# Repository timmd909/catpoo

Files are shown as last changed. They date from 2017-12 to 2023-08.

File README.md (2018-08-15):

# Cat Antagonizing Tactical Platform of Oppression (CATPOO)

This project is for my autodidactic hacking pleasure. One of my childhood
dreams was to create a robot like a T-800. One day...

In the meantime, figured it wouldn't be too hard to create a robot that
can antagonize and annoy cats or small dogs.

## Related Repositories

* [CATPOO Drive](git@github.com:timmd909/catpoo-drive.git) - Software
  for Arduinos for controlling all robots.
* [CATPOO Models](git@github.com:timmd909/catpoo-models.git) - FreeCAD
  models of everything necessary to build a CATPOO.

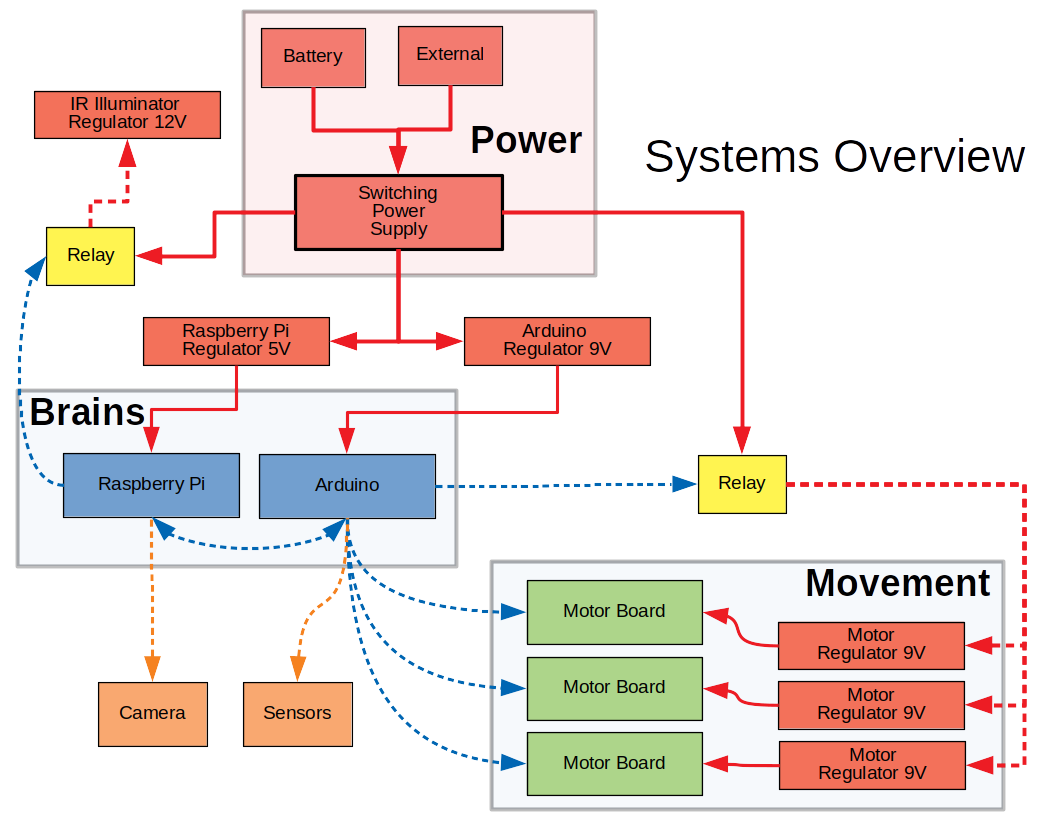
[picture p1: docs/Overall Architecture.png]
Overall architecture


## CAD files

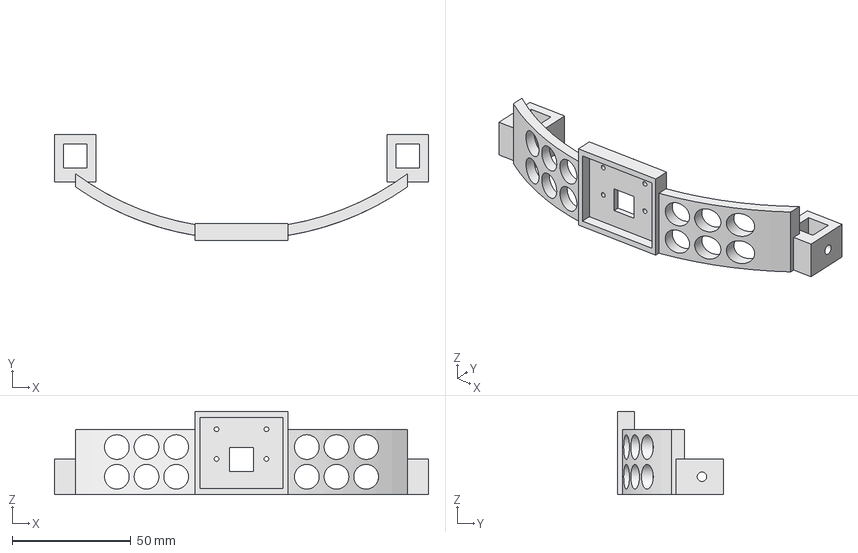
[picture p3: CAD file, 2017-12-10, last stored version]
docs/models/Camera and illuminator.fcstd
157.5 x 44.5 x 35.0 mm

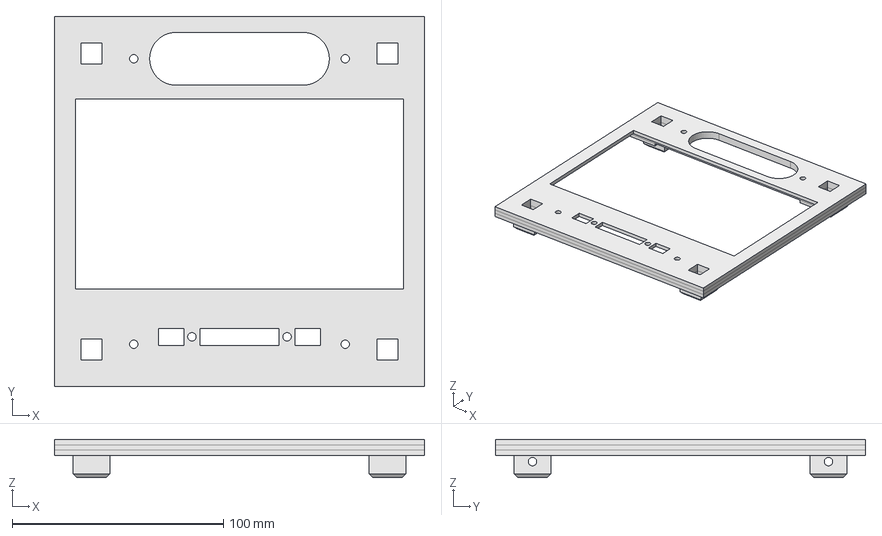
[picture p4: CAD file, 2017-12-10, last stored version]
docs/modular/LCD - top redone.fcstd
175.0 x 175.0 x 18.0 mm

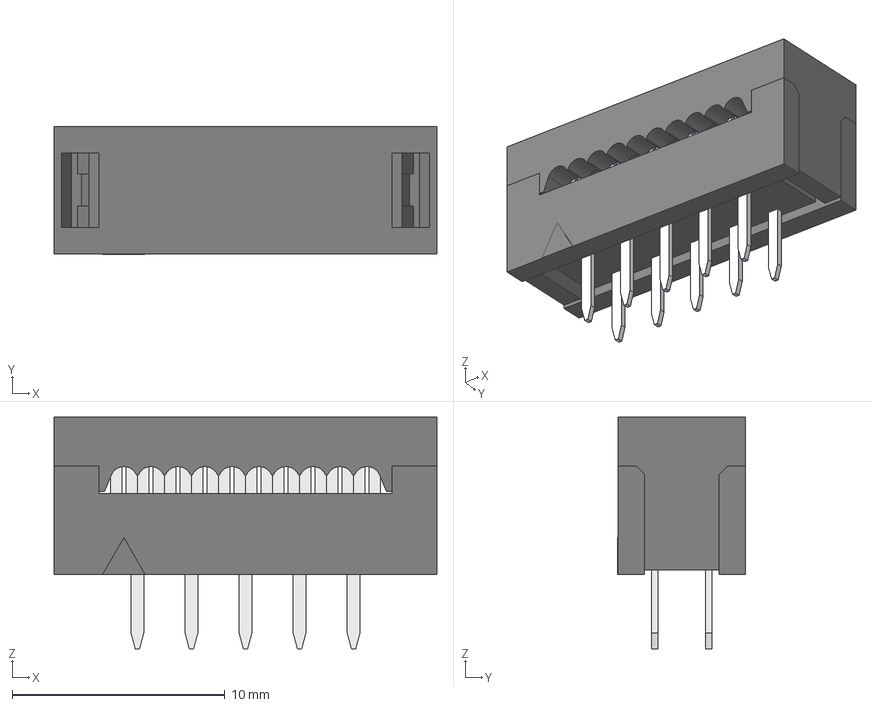
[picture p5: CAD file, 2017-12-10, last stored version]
docs/parts/connectors/direct-wire-2x5.stp
18.0 x 6.03 x 10.9 mm

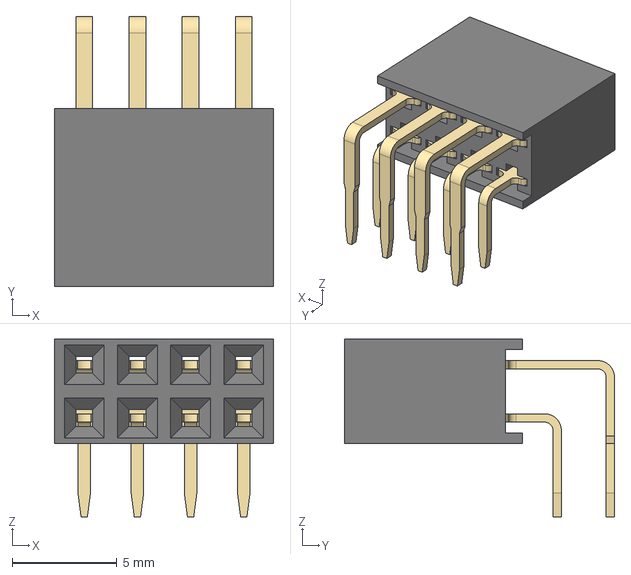
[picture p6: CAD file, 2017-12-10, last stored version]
docs/parts/connectors/female/right_angle/2.54mm/DS1024-2x4RF1.stp
10.5 x 12.9 x 8.50 mm

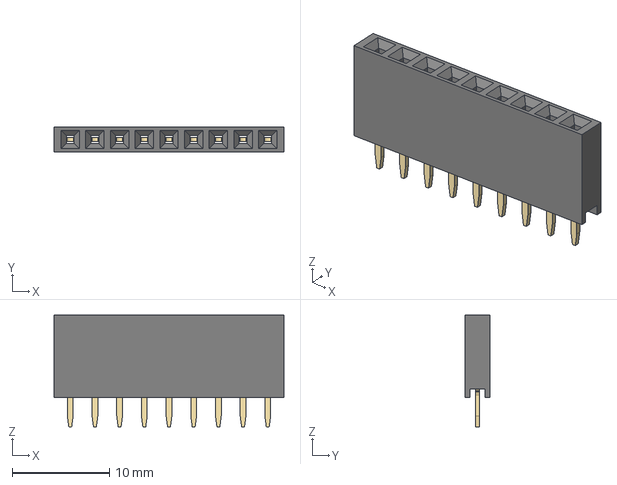
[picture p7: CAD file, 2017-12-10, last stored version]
docs/parts/connectors/female/vertical/2.54mm/DS1023-1x9SF11.stp
23.7 x 2.54 x 11.5 mm

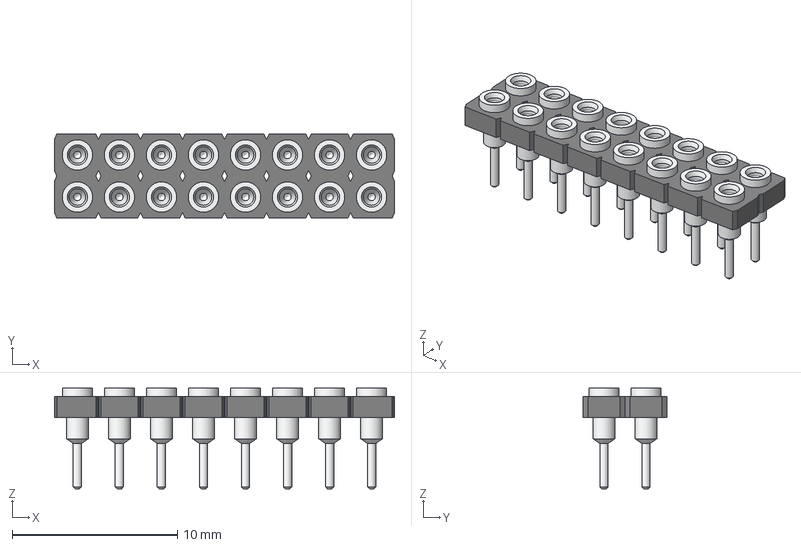
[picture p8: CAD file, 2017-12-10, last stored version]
docs/parts/connectors/female/vertical/2.54mm/Samtec/SDL-108-TT-11.stp
20.6 x 5.08 x 6.10 mm

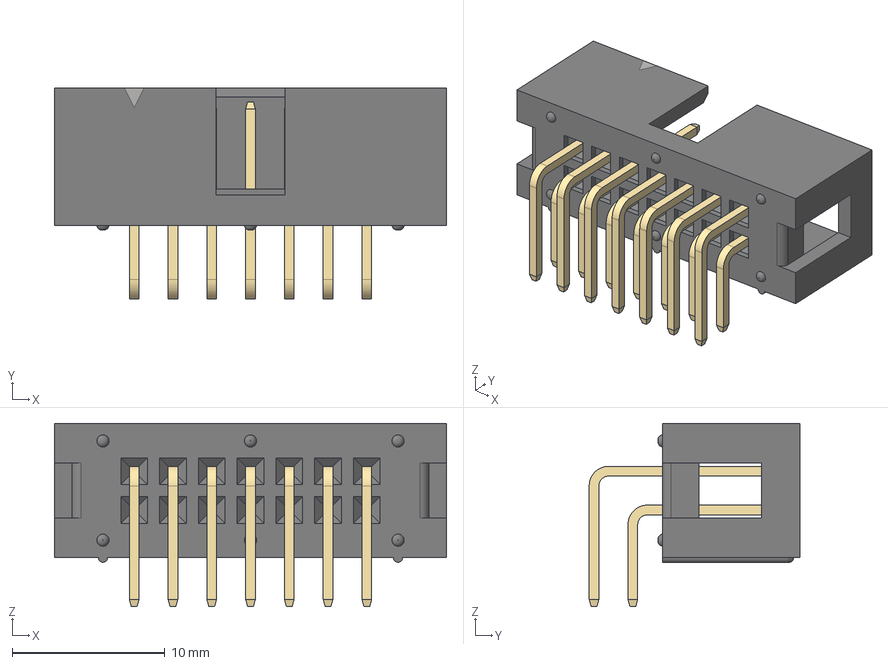
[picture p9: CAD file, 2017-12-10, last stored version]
docs/parts/connectors/male/shrouded/right_angle/2.54mm/DS1013-14RSiB.stp
25.7 x 13.8 x 12.0 mm

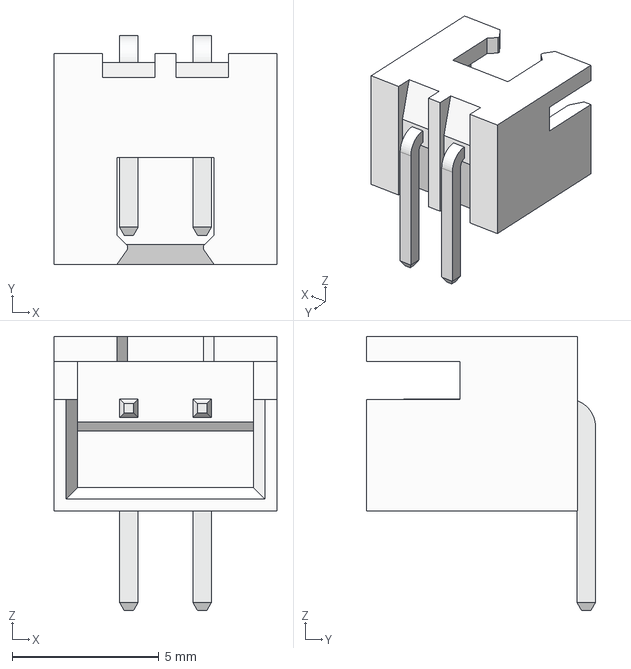
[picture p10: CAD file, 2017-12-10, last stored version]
docs/parts/connectors/male/shrouded/right_angle/2.5mm/DS1069-2MRW6XB.stp
7.60 x 7.82 x 9.35 mm

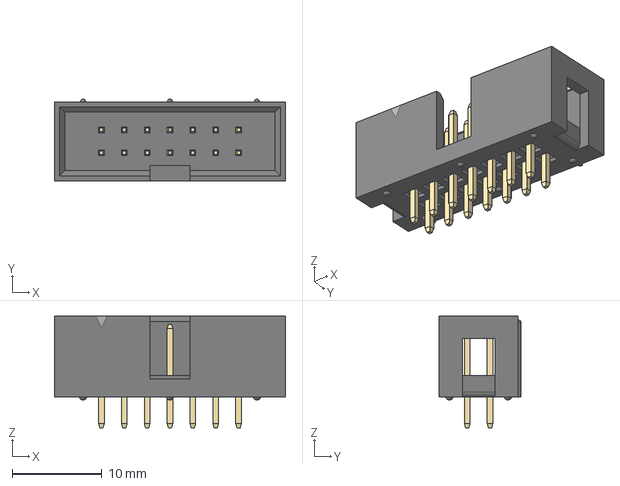
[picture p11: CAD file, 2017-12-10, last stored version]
docs/parts/connectors/male/shrouded/vertical/2.54mm/DS1013-14SSiB.stp
25.7 x 9.10 x 12.4 mm

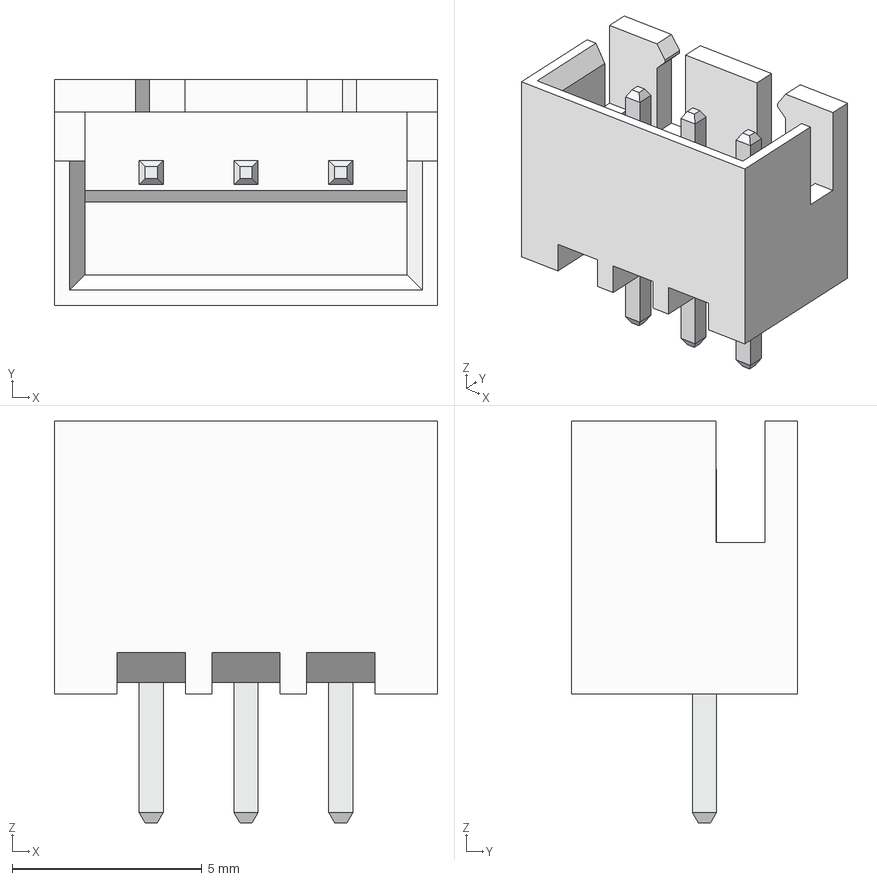
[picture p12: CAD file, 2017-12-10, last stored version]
docs/parts/connectors/male/shrouded/vertical/2.5mm/DS1069-3MVW6X.stp
10.1 x 5.95 x 10.6 mm

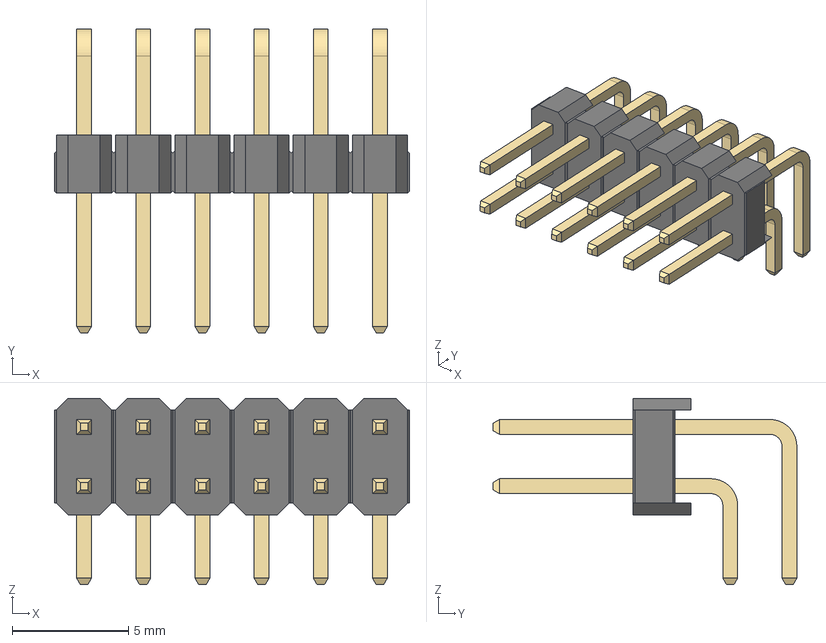
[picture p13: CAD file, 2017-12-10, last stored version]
docs/parts/connectors/male/unshrouded/right_angle/2.54mm/DS1022-2x6RF11.stp
15.2 x 13.0 x 8.00 mm

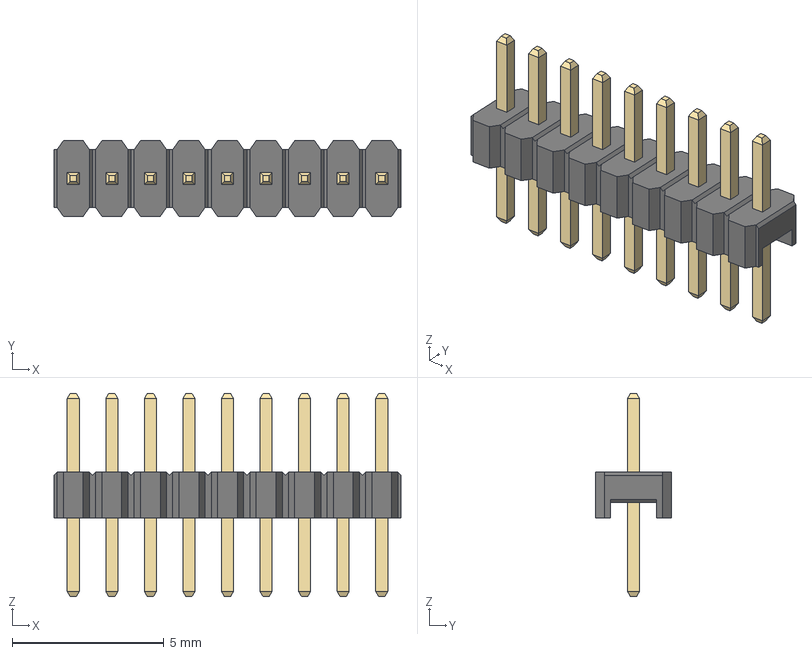
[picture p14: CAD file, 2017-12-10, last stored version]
docs/parts/connectors/male/unshrouded/vertical/1.27mm/DS1031-01-1x9P8BV2-1.stp
11.4 x 2.50 x 6.70 mm

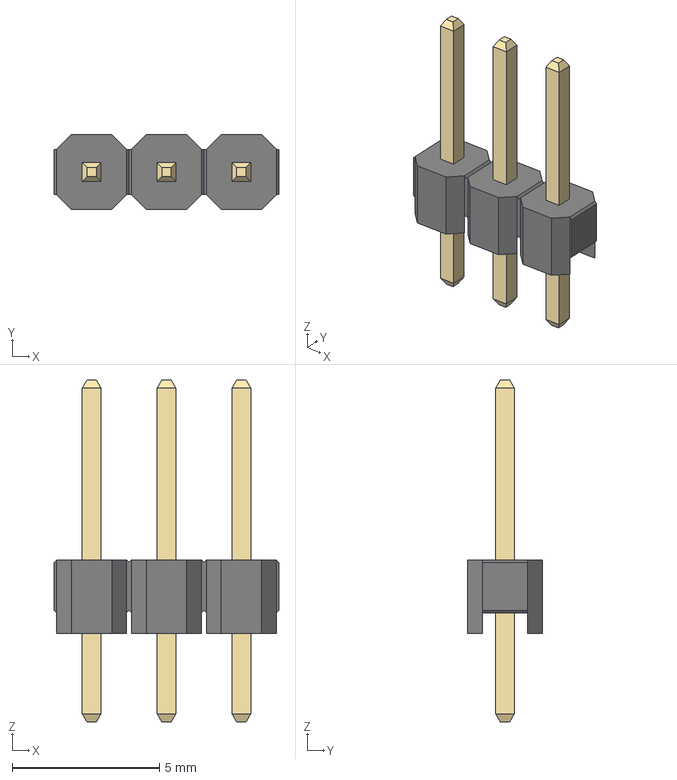
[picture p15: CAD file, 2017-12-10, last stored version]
docs/parts/connectors/male/unshrouded/vertical/2.54mm/DS1021-1x3SF11.stp
7.62 x 2.54 x 11.6 mm

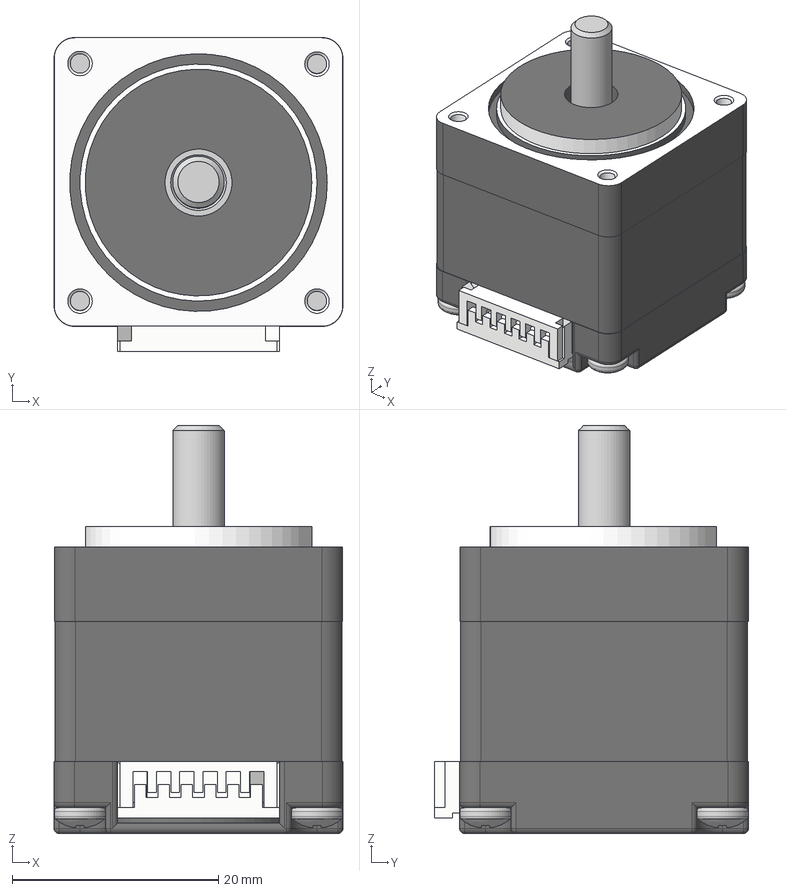
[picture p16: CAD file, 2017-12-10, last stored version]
docs/parts/NEMA 11 Stepper Motor.STEP
28.0 x 30.5 x 39.6 mm
Bottom Cap
695-ZZ Bearing x 2
Centre Housing
Top Cap
Rotor
Rotor Washer
Short Spacer
Long Spacer
M2.5 x 20mm Bolt x 4

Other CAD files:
docs/models/LCD bottom.fcstd
docs/modular/10 hole connector.stl
docs/parts/10mm LED.stl
docs/parts/connectors/direct-wire-2x8.stp
docs/models/30mm adapters.fcstd
docs/models/30mm slim adapters.fcstd
docs/models/30mm tri-adapter.fcstd
docs/models/Arduino support.fcstd
docs/models/Battery.fcstd
docs/models/Jack.fcstd
docs/models/LCD top.fcstd
docs/models/Motor drivers.fcstd
docs/models/Raspberry Pi.fcstd
docs/models/Regulators.fcstd
docs/models/Rib vertical support.fcstd
docs/models/Rib.fcstd
docs/models/Rod - 10 hole.fcstd
docs/models/Rod - 15 hole.fcstd
docs/models/Rod - 21 hole.fcstd
docs/models/Rod - 7 hole.fcstd
docs/models/Stand.fcstd
docs/models/T-Cobbler support.fcstd
docs/models/Vex wheel adapter.fcstd
docs/modular/110-140 adapter.stl
docs/modular/140-110 adapter.fcstd
docs/modular/15 hole connector.stl
docs/modular/7 hole connector.stl
docs/modular/Camera mount.fcstd
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

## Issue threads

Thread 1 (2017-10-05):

Wire up Pi & Arduino via I2C

timmd909, 2017-10-05:
# Overview

I tried doing USB communication, but every now and then the Pi would come up on the wrong serial port. That was annoying. Didn't try old fashioned serial as I'd imagine the same sort of shit would happen again. I2C would also allow me to keep things as small as possible.

# Goals

* [ ] Purchase more [wires with pre-crimped terminals](https://www.pololu.com/category/71/wires-with-pre-crimped-terminals) and [connector housings](https://www.pololu.com/category/70/crimp-connector-housings).
* [ ] Set up Arduino and Raspberry Pi like how it's described the [the tutorial](https://oscarliang.com/raspberry-pi-arduino-connected-i2c/).
* [ ] Verify that characters sent are echoed back and that the LED toggles

# Resources

* https://oscarliang.com/raspberry-pi-arduino-connected-i2c/

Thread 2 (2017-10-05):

Stepper Motor Circuit Design and Hookup

timmd909, 2017-10-05:
# Goals

* [ ] Circuit design
* [ ] Only 1 cable should be coming out of the drive platform. Candidate cables:
  * [6 conductor ribbon cable](https://www.pololu.com/product/972) with [2x6 pin headers](https://www.pololu.com/product/854) on the boards we're connecting. We don't need all 6, but it can only be inserted one way.
  * [2x5 crimp connector housing](https://www.pololu.com/product/1913)
* [ ] Arduino board sits on top of female headers to a circuit board
  * Solderless breadboards are wasteful! (in a space sense)
  * [ ] 4 blocks of 1x4 0.1" female headers for each servo
* [ ] Servos are hooked up to Arduino
  * [ ] Servos are connected with [precrimped wires with male ends](https://www.pololu.com/category/71/wires-with-pre-crimped-terminals) in [1x4 housings](https://www.pololu.com/product/1903)
    * [ ] Buy [12" with male and female ends](https://www.pololu.com/product/1855), and then cut them all in half for splicing and soldering.
      * [ ] Green - Col 1
      * [ ] Blue - Coil 2
      * [ ] Red - Coil 2
      * [ ] Black - Col 1
  * [ ] Wires from servo to Arduino should not need to be more than 150mm. (Robot is ~200mm on all sides)
* [ ] Arduino is able to drive all 4 wheels independently
  * Could be a program as simple as having one motor turn one way for a sec, then the opposite, before cycling to the next motor.
  * Main point is to confirm motor function and no bad wires

# Connector Wiring

|  x | 0      | 1             | 2             | 3       |
|----|--------|---------------|---------------|---------|
|  0 | +5V    | **Serial Tx** | *Serial Rx*   | Ground  |
|  1 | Ground | *Serial Rx*   | **Serial Tx** | +5V     |

timmd909, 2017-12-13:
went with the KISS principle instead

Closed 2017-12-13.

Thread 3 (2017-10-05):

Drive Protocol Design & Implementation

timmd909, 2017-10-05:
Once #1 and #2 are done, it's time to actually get them servos moving.

# High Level Goals

* [ ] From the Raspberry Pi, I want to be able to send [Logo like commands](https://en.wikipedia.org/wiki/Logo_(programming_language))
  to the robot. (Play around Logo: [papert](http://logo.twentygototen.org/))
* This is a version 1 kind of API and shouldn't be able to do everything.
  Manually controlling individual motors shouldn't be allowed.
* [ ] Limit the speed of the motors to 1 revolution per second or slower
  * 1 revolution per second = 200mm = 0.2m/s (roughly and good enough for me)
  * At that speed, the robot would coverage about a meter in 5 seconds. That
* The total distance traveled per rotation is about 200mm with the wheels
  that I have now. (Assuming the wheels are ~60mm. I haven't measured them.)
  actually might be too fast...

# Drive Protocol

* [ ] All commands must end with a newline
* [ ] Good commands will return in `OK` being sent back over the wire unless
  otherwise specified.
* [ ] Bad commands are echoed back to the Pi like so:
  * [ ] On unrecognized command or parsing error: `ERROR: $WHATEVER-THE-COMMAND-WAS`
    (ex: `ERROR: FOOWARD 100` because `FORWARD` wasn't spelled right)
  * [ ] If the command queue is full, then `QUEUE_FULL` should be returned
* [ ] Commands than can be queued: `RESET`, `SPEED`, `GET`
* [ ] Commands than run immediately: everything else

## Terminology

* `Idealized step` - Instead of 200 or whatever number of steps per 360°,
  let's instead think of the number of rotations.

## Arduino Exportable States

These values can be accessed from the Pi by sending a `GET` command
(ex: `GET NUM_QUEUED` would return the number of queued commands).

* `SPEED` - Current speed. Defaults to `1`.
* `MAX_SPEED` - Maximum speed (capped at `100`). Any time a `SPEED` over
  `100` is specified, it'll be capped to this value.
* `MAX_DISTANCE` - Maximum distance a command will honor. Anything over this
  value is capped.
* `CURRENT` - Get the current executing command (Ex: `FORWARD 1000`). If no
  commands are executing, it returns `IDLE`
* `NUM_QUEUED` - Number of queued commands
* `MAX_QUEUED` - Maximum number of commands to queue before rejecting new ones.
  Set to `4` at the beginning

## Proposed Commands

| Commands             | Description                                            |
|----------------------|--------------------------------------------------------|
| `RESET`              | Halt all movement and reset everything (speed, queue, etc).
| `FORWARD m`          | Where `m` is the distance in millimeters
| `BACKWARD m`         | Where `m` is the distance in millimeters
| `SPEED n`            | How fast should the robot go
| `LEFT d`             | Rotate the robot along the vertical axis by `d` degrees
| `RIGHT d`            | Rotate the robot along the vertical axis by `d` degrees
| `STRAFE_LEFT m`      | Strafe to the left `m` millimeters
| `STRAFE_RIGHT m`     | Strafe to the right `m` millimeters
| `CIRCLE_STRAFE r d`  | The ultimate shooter move for circling around a target.
| `GET v`              | Get Arduino interval value `v`. (See Arduino Exportable States above)

### Moving Forward/Backward and Rotating Notes

With the `FORWARD` and `BACKWARD` commands, the conversion from mm/s to steps
is pretty easy. With rotation, that's a bit more difficult. The circle the
wheels would travel would be about 600 mm. So `SPEED 100` and `LEFT 360` would
take 6 seconds to rotate.

### Circle Strafe Uber Mode Notes

`CIRCLE_STRAFE` will be an awesome way to get photos of something from
every angle. Wouldn't it be cool if I could automatically scan something
and convert it to a 3d model?

The radius of an imaginary circle the robot will rotate around is defined
by `r`. If `r` is positive, the center of rotation is in front of the robot
and thus the camera always points to center. If negative, the central point
will be behind the robot and the camera will always face out. The radius
is the distance from the center of the robot, thus a radius of `100` would
rotate around the camera suitable for a 360 camera view.

The total number of degrees to rotate around the object is `d` (so `360`
would do 1 full loop, `720` would circle it twice, etc). Negative values
would cause the robot to go clockwise around the object when viewed from
above. Positive values would be counterclockwise.

timmd909, 2017-12-13:
moved to https://github.com/timmd909/catpoo-drive/issues/1

Closed 2017-12-13.

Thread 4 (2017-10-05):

CAD Design of drive platform

timmd909, 2017-10-05:
* [x] Platform should be 200mm x 200mm x 50mm or smaller.
* [x] Must have some sort of dock or interlocking system on top
* [ ] Only 1 cable should be coming out of the bottom that include power and rx/tx

timmd909, 2017-12-13:
fuck only 1 cable... went w/ a cacophony of wires instead. Each driver requires 6 wires going to it for a total of 24 wires.

Closed 2017-12-13.

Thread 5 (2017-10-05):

Connections and Modularity

timmd909, 2017-10-05:
# Miscellaneous

* Powering and connecting everything via USB connectors wastes too much space and won't work in the new form factor.

# Themes

* Shrouded Headers on boards, with ribbon cables connecting them
  * Headers
    * [2x3](https://www.pololu.com/product/854)
    * [2x8](https://www.pololu.com/product/898)
  * Ribbon Cables
    * [2x3](https://www.pololu.com/product/972)
    * [2x8](https://www.pololu.com/product/973)

# Custom Shield for Raspberry Pi

* Would also serve as a power distribution point
* Could be connected to the Pi via [0.1" connector housing](https://www.pololu.com/product/1992) with [precrimped female wires](https://www.pololu.com/product/1930)
  * Could use the T Cobbler (if I still have it)
* Connectors
  * Battery in (straight from the battery or whatever)
  * Some special kind of connector for the motors & Arduino and any power it needs (9v-12v I'm guessing)
  * 2x20 connector to Raspberry Pi for power and I/O
  * For the range finders, if I'm doing it off the Arduino, the API will need updated in #3.
    * If the Pi is doing it, then I'll need [something like this](https://www.adafruit.com/product/856) and [know how to do it](https://learn.adafruit.com/raspberry-pi-analog-to-digital-converters/overview)
    * Putting the range finding in the drive is attractive because I can put in greater protections against doing something stupid. In case the Pi sends a terrible, I can reject it. Think: don't allow the Pi to have it smash into a wall repeatedly.
    * ETOH and any other stupid sensors I can put on could be hooked up to the Pi no problem. Maybe a mixed approach would be best...

# Main Module Connections

* body - drive train and sensors
  * Needs 6v+ and 5v+ for motors, controllers, and Arduino
* main bus - Powers all other portions. The custom shield will serve this purpose
  * Battery in
  * 5v out for:
    * Raspberry Pi
    * Arduino
    * Stepper controllers
  * 6v+ out for:
    * stepper motors
    * Display
* brain - Raspberry Pi. More of the cerebrum than anything else
* visual - Touch screen LCD for displaying brain state
  * Not necessary for initial design, but body must allow a display to be placed on top.
  * Already has power and HDMI out.
  * Power will come from main bus
  * HDMI goes straight to Raspberry Pi

# External Connections and Sensors

* [USB panel mount](https://www.adafruit.com/product/908)
* [Ethernet panel mount](https://www.adafruit.com/product/909)
* [DC barrel jack panel mount](https://www.adafruit.com/product/610)
* [IR Range finder](https://www.pololu.com/product/136) - left and right
* [Sonar Range finder](https://www.pololu.com/product/723) - not sure if that's the exact one, but good enough for mechanicals/reference

timmd909, 2017-11-01:
moved to https://github.com/timmd909/catpoo/wiki/Connections-and-Sensors

Closed 2017-11-01.

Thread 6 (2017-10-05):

Sensor & Peripheral Device Aquisition

timmd909, 2017-10-05:
# Required

* [x] 1 sonic range finder for forward distance measurement
* [x] 2 IR range finders for the sides
* [ ] 1 range finder for the back
* [ ] Some sort of kill switch to hit in a panic [like this $6 switch](http://www.robotshop.com/en/emergency-stop-switch.html)
* [ ] [Small speaker](http://www.robotshop.com/en/mini-external-usb-stereo-speaker.html)
    * Can be anything as long as it can be hooked up to the Pi easily
    * [These ones](http://www.robotshop.com/en/usb-powered-speakers.html) for $10 might be a bit too large... but maybe could be mounted on the outside on the sides?
    * [Audio amplifier board](https://www.amazon.com/DROK-Amplifier-Dual-channel-Amplifiers-Potentiometer/dp/B01ER1X450/ref=sr_1_14) would also be acceptable.

# So Cheap I Should Add it

* [ ] [Accelerometer](http://www.robotshop.com/en/adxl345-bb-3-axis-accelerometer-module.html) ($5)
  * Or [this one that has a compass](http://www.robotshop.com/en/lsm303d-3-axis-accelerometer-compass.html) $8
* [ ] [Temperature sensor](http://www.robotshop.com/en/temperature-sensor-tmp36.html) ($1.50)
  * Or [this one w/ humidity sensing](http://www.robotshop.com/en/gravity-dht11-temperature-humidity-sensor.html) $5
* [ ] [Light sensor](http://www.robotshop.com/en/mini-photocell-light-sensor.html) ($1.50)
* [x] ETOH sensor (already have it)

# Would Be Cool

* [ ] Temperature sensor
* [ ] [digital vibration sensor](http://www.robotshop.com/en/gravity-digital-vibration-sensor.html) - The robot could activate when it sense vibrations or being poked. Could really fuck w/ a cat if the robot suddenly came alive soon as it gets close
* [ ] Some way to detect when the robot bumps into something. Maybe use some [roller switches](http://www.robotshop.com/en/spdt-roller-lever-micro-switch-2pk.html) behind a bumper?
* [ ] [Air quality sensor](http://www.robotshop.com/en/air-quality-breakout-board-ccs811.html) Wouldn't it be cool if the robot could tell the difference between a smoke filled bar and a clean room? Fake coughing whenever it detects smoke would be hilarious
* [ ] [Heart rate sensor](http://www.robotshop.com/en/pulse-heart-rate-sensor-arduino.html) this is completely useless for anything that I'd like to do, but it's cool... so it's going on the list

timmd909, 2017-10-18:
moved to https://github.com/timmd909/catpoo/wiki/Sensors

Closed 2017-10-18.

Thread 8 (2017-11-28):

Things Left to Buy

timmd909, 2017-11-28:
Time to start buying the last bit of electronics! Looks like it will be functional after this!

For the connections, simple is best. With the colored headers, and matching colored cables, how to connect everything will be unambiguous.

* [x] Screws and nuts
    * [x] 1 × [#1067 - Machine Hex Nut: #4-56 (25-pack)](https://www.pololu.com/product/1067)
    * [x] 6 × [#1068 - Machine Hex Nut: #4-40 (25-pack) ](https://www.pololu.com/product/1068)
    * [x] 1 × [#1966 - Machine Screw: #4-40, 3/4″ Length, Phillips (25-pack)](https://www.pololu.com/product/1966)
    * [x] 4 × [#1963 - Machine Screw: #4-40, 1" Length, Phillips (25-pack)](https://www.pololu.com/product/1963)
    * [x] 4 × [#1962 - Machine Screw: #4-40, 1/2″ Length, Phillips (25-pack)](https://www.pololu.com/product/1962)
    * [x] 4 × [#1966 - Machine Screw: #4-40, 3/4″ Length, Phillips (25-pack)](https://www.pololu.com/product/1966)
* [x] Male headers
    * [x] 2 × [0.100" (2.54 mm) Breakaway Male Header: 1×40-Pin, Straight, Black](https://www.pololu.com/product/965)
    * [x] 2 x [0.100" (2.54 mm) Breakaway Male Header: 1×40-Pin, Straight, Red](https://www.pololu.com/product/2665)
    * [x] 2 × [0.100" (2.54 mm) Breakaway Male Header: 1×40-Pin, Straight, White](https://www.pololu.com/product/2664)
* [x] Pre-Crimped Terminals
    * [x] 2x [Wires with Pre-Crimped Terminals 5-Pack M-F 24" Black](https://www.pololu.com/product/1880)
    * [x] 2x Wires with Pre-Crimped Terminals 5-Pack M-F 24" Red
    * [x] 2x Wires with Pre-Crimped Terminals 5-Pack M-F 24" White
* [x] Crimped Connector Housings
    * [x] 1 × [0.1" (2.54mm) Crimp Connector Housing: 1x1-Pin 25-Pack](https://www.pololu.com/product/1900) (everything else)
    * [x] 1 × 0.1" (2.54mm) Crimp Connector Housing: 1x2-Pin 25-Pack (power only)
    * [x] 1 × 0.1" (2.54mm) Crimp Connector Housing: 1x3-Pin 25-Pack (for sensors)
    * [x] 1 × 0.1" (2.54mm) Crimp Connector Housing: 1x4-Pin 25-Pack (for motor drivers)
* [x] Female headers
    * [x] 2 × 0.100" (2.54 mm) Female Header: 1x20-Pin, Straight (For T Cobbler)
    * [x] 2 × [0.100" (2.54 mm) Female Header: 1x17-Pin, Straight](https://www.pololu.com/product/1111) (for Arduino)
* [ ] Assorted hookup wires
    * [ ] Red 24 gauge stranded wire
    * [ ] White 24 gauge stranded wire
    * [ ] Black 24 gauge stranded wire
* [ ] [Raspberry Pi heatsinks](https://www.amazon.com/Easycargo-Raspberry-Heatsink-Aluminum-conductive/dp/B07217N5LS)

timmd909, 2017-12-03:
holding off on the heatsinks and wire. Think I have enough...

Closed 2017-12-03.

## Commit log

2014-02-08 Adding in my starting off settings for the servos n at
2014-03-03 Adding icons for the front/back and updates to back face
    The funny part is, I'm probably not going to use any of this and just drill holes where needed.
2014-03-03 Wrote simple program to capture and save frames to a temporary file
    Next step: send to SHM
    after that: send out via PHP
2014-03-03 Dammit, autotools… so many files
2014-03-03 Invalid camera settings now throw custom exception
2014-03-18 Adding info on the servo controller settings
2014-03-18 Adding testing script for controlling servos with PHP
2014-03-23 Clamping values to sane ranges
2014-03-23 whoopsie… didn't finish that refactor
2014-04-02 Switching to using C++ for motion control.
    I'd rather brush up on C++ more.
2014-07-12 Not sure what this was…
    taking a month off from the project and not having everything committed
    was a bad idea lol
2014-07-12 added a couple second delay for DHCP to finish
2014-07-12 Updated servo offsets
2014-07-12 Adding in ability to use arrow to navigate.
    so preliminary tests should this won't work until I use a proper serial
    library or other to speak to the servo controller
2015-05-13 Rough drafts for laser cutting
2015-05-13 Redoing the design of the box
    Screw having a brain design that's modular... might
    as well just recut the body whenever I need a new
    design. Since I won't be relying on eyeballing while
    drilling and lots of hot glue, this should work better.
2015-05-14 Update robot body design
    Pretty sure this is the final design at this point.
    There's a billion holes at standard sizes that can be
    easily expanded if necessary. If this doesn't work,
    I dunno what will... :-)
2015-06-19 Add in circle robot chassis design, round #1
2015-06-19 Bottom circle almost done of new chassis :-)
2015-06-19 Updating circle chassis and adding sonar link
2015-06-23 Please, oh please, be the final cut
2015-06-24 Last minute adjustments 2 chassis
    Damn bolt is blockish :-(
2015-07-31 Why did I forget to add Grunt CLI?
    I might as well be smashed everytime I try to code...
    which will probably not be the case for 11 months so
    I will need to look for better excuses.
    Maybe lack of Mt Dew?
2015-09-07 Remove old server x4 configuration
    I'm glad I'm going w/ the 2 servos w/ the track
    instead of 4 separate wheels. Things have been much
    easier since :-)
2015-09-11 Browser is operational now
    Time to charge the battery and test it out!
2015-09-19 Staring on new robot chassis design
    I just really like using laser cutters... I admit.
2015-09-20 Adding more facets to the new case
2015-10-17 Ready to cut!
2015-10-22 Ready to cut tomorrow!
2015-10-22 Ignore Brackets extension settings
2015-10-24 Final tweaks to cut
2015-10-24 W00t! Arduino -> JSON -> Serial -> Pi
2016-03-21 Update web UI, add brighten button
2016-03-21 Remove old schematics
2016-03-21 Add notes on Arduino,low-level issues
2016-03-21 Final cut of octogon design
2016-03-30 Add final cut design
2016-04-03 Tweaks to recut
    Going to use etching for the logos this
    time. Also, I'm labeling the shit out of
    everything to avoid a misglue like next
    time. Note: the rubbing alcohol works
    great to take apart the hot glue.
2017-12-10 Add prototype 3D models
    [10 hole connector.stl, 10mm LED.stl, 110-140 adapter.stl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]
2017-12-10 Rearrange docs
    Moved models to the `catpoo-models` repo
    [10 hole connector.stl, 10mm LED.stl, 110-140 adapter.stl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]
2018-04-28 Add in Ansible provisioning into catpoo directly
    It'd be confusing to someone else to have to switch over to
    izanagi thing to image a robot.
2018-05-19 Add controller code
    This will be on the Raspberry Pi and called by the web server
2018-05-21 update submodules before bed
2018-05-22 Add circuits submodule
2018-05-23 Update circuits submodule
2021-04-04 Update circuits
2021-07-31 Remove old circuit submodule
